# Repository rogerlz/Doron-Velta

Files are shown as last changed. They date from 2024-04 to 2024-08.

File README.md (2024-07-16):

# Doron-Velta

## What's This?

I've never owned a Delta printer, but their unique design and mechanics have always fascinated me. As some of you may know, I contribute to maintaining [Danger-Klipper](https://github.com/DangerKlippers/danger-klipper), which involves testing various configurations and setups. In support of this work, Imac_29 (from the #pasteldenata) generously gifted me an FLSUN Q5. Interestingly, it never even saw the light of day in my home; I disassembled it on the very first day.

This all happened around SMRRF2023, where we humorously speculated that the Voron Design team would never release an official Delta design. What could be a better April Fool's joke than that? So, I went with it.

Originally, the plan was to create an April Fool's prank using the FLSUN Q5, printing parts to make it look like a Voron design. However, I ended up using just the Q5's arms and nothing else. I gathered a collection of spare parts I had lying around, began measuring, and started designing in CAD. After various splits and merges, I had a design reminiscent of the Voron Trident that I was happy enough. It wasn't complete but enough to share with other contributors.

[DoubleT](https://github.com/3DPrintingMods) was immediately on board and decided to build one himself. Within hours of discussing it with me, he had already ordered half of the parts. Interestingly, he managed to get his version printing even before I did.

I want to make it clear that I don't claim to have extensive CAD expertise or experience with Delta printers for this project, so please take my work with a grain of salt. My primary aim was, and remains, to explore Klipper firmware with Delta kinematics.

Yes, the printer works. Yes, it prints. Yes, it's aesthetically pleasing. And yes, it's far from being a perfect design. Most importantly, no, **this is not an official project by Voron Design**.

## **** Disclaimer ****

The toolhead doesn't have the full bed travel. It will hit the panels and/or the belts. New interactions of the printed parts will improve this, but I can't promise it will ever have the full bed travel without a major redesign.
I appreciate any and all the feedback, but I want to ensure everyone understands the design limitations.

## Links

[Doron-Velta Early Bird Kit by FYSETC](https://s.click.aliexpress.com/e/_DejsxX9)\
\
[DV-000 by rogerlz](https://www.reddit.com/r/voroncorexy/comments/1bsr2d7/special_serial_request_dv000_rogerlz/) ([YouTube](https://www.youtube.com/watch?v=DuFxvsZ5HEU))\
[DV-001 by DoubleT](https://www.reddit.com/r/voroncorexy/comments/1bsrmby/special_serial_request_dv001_doublet/) ([YouTube](https://www.youtube.com/watch?v=adXSPTnKe_0))\
[DV-002 by Robert Klotz](https://www.reddit.com/r/voroncorexy/comments/1cw2izk/special_serial_request_dv002_robert_klotz/)\
[DV-003 by Xiar](https://www.reddit.com/r/voroncorexy/comments/1d45y17/special_serial_request_dv_xiar/)\
[DV-004 by Owl47 Bruno Silva](https://discord.com/channels/825469421346226226/1246869064173748285/1246998381964824697)\
[DV-005 by ZombieHedgeDog](https://discord.com/channels/825469421346226226/1246869064173748285/1247178407012208701)
...

## Pictures

 
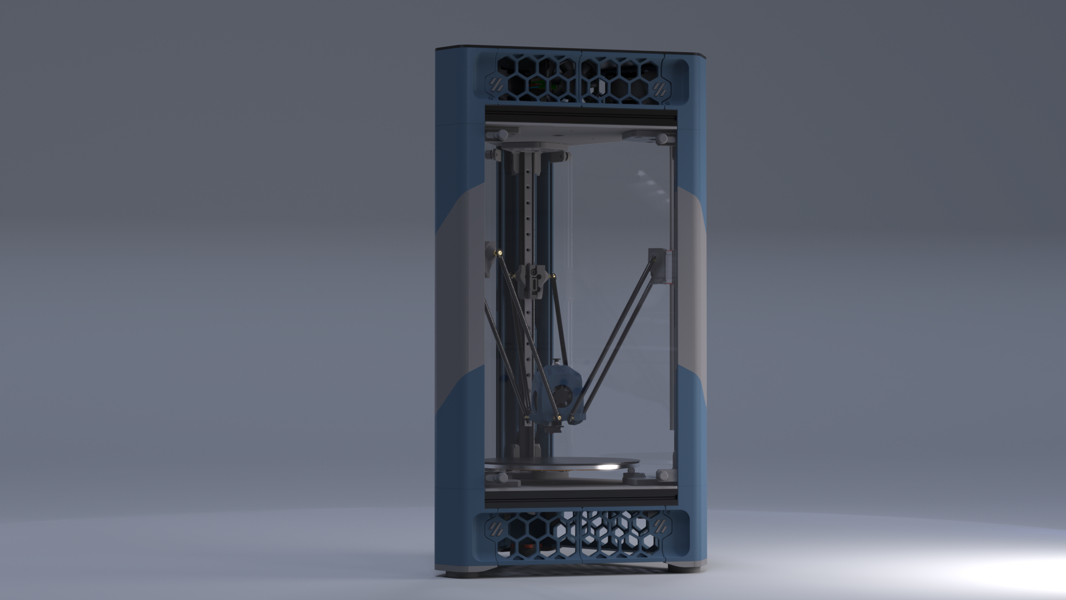
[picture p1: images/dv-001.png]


## Bill of Materials (BOM)
A bill of materials can be found here: [BOM](./BOM.md)

## Changelog

July 13, 2024 (R2 v20)
  - I got an extra ~10mm travel achieved with some improvements on the printed parts. The 2020s moved 5mm to the back, and 2040s moved 5mm to the sides. Almost all printed parts are changing, except the skirts. The only hardware changes are on the ACM panels as they are slightly wider now. The M5x60s are no longer needed.
  - Doron-Velta has a new logo (thanks to @matrixray).
  - I added new skirts with the new logo.
  - There is also a new skirt with a 6020 fan (Thanks to @timmit99 and @seti118 for the fan mount)
  - New UHP-200 mount to compensate the extrusions movement (Thanks to @timmit99)
  - The official toolhead is now [CraneFly by chirpy](https://github.com/chirpy2605/voron/tree/main/general/CraneFly). The MiniSB is hidden in the F3D file, but I won't be making changes to it anymore. Thanks chirpy!
  - Lots of small tweaks here and there based on the community feedback. Thanks everyone.

June 7, 2024 (R1 v30)
  - The interactions are on fire. I invite you to join the DOOMCUBE Discord (#doron_velta_dev) or the Voron Discord (Doron Velta thread) to chat with more people building and modding the design.
  - I got an extra 5mm travel by removing some meat from the belt carriages. That means a new idler mount, new carriage and new endstop mount. No hardware changes.
  - I removed the SKR Pico and Raspberry Pi objects to reduce the cad file size.
  - This makes the Release 1 version with the exported STLs.

June 1, 2024 (v23)
  - Quality of life changes everywhere. Chamfers, fillets, and hole sizes are better now, but nothing major has changed that I would recommend reprinting.
  - @kyleisah was kind enough to create built-in supports for the corner pieces. Thank you!
  - @chirpy is working on an amazing new toolhead. Check it out here [here](https://github.com/chirpy2605/voron/tree/main/general/CraneFly). Thank you!

April 27, 2024 (v16 I think)
  - I modified the Nema17 mounts to include a slot for an MR625 bearing and access to the pulley grub screw. I duplicated them to the bottom for those interested in doing AWD.
  - A new bottom panel and a few missing chamfers were added.

## Thanks to

This was a fun project, and I have a lot of people to thank for, especially the VD (Voron Discord) contributors.

A heartfelt thanks goes out to DoubleT, who dedicated countless hours to CAD work, surpassing even my own time, and to Zruncho, whose guidance, support, and encouragement through direct messages and voice chats were invaluable.

I also want to extend my appreciation to pnewb, clee, hartk, Tetsu, Kyleisah, diem, imac_29 and many others for their support and contributions – you all have my sincerest thanks <3.

I would like to give special acknowledgment to the vendors: [Lab4450.com](https://lab4450.com) for supplying electronic components; ffb (Discord: ffb_9195) and [Seti](https://viperworx.uk) for supplying the PC and ACM panels; and [MandalaRoseWorks](https://mandalaroseworks.com) for the custom-made and beautiful Alu bed.

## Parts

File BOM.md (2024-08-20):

## Doron Velta Bill of Materials (BOM)

### Frame:

| Part | Qty | Notes |
| - | - | - |
| HFSB5-2020-500-TPW  | 3 | Part number is for ordering from Misumi |
| HFSB5-2040-235 | 6 | Part Number is for ordering from Misumi |

### Bed Components:

| Part | Qty | Notes |
| - | - | - |
| 200mmø x 5mm Aluminum Bed | 1 | [MandalaRoseWorks](https://mandalaroseworks.com/collections/doron-velta) / EU folks can ping @owl47_brunosilva on Discord |
| 200mmø PEI Sheet | 1 | [Aliexpress](https://s.click.aliexpress.com/e/_DCjuren) |
| 200mmø Magnetic Sheet | 1 | - |
| M3 x 9mm Ball Screw | 3 | [Aliexpress](https://s.click.aliexpress.com/e/_DkTj85h) |
| 3 x 20mm Steel Dowel Pin | 6 | [Aliexpress](https://s.click.aliexpress.com/e/_DkNIN0x) |

### Motion Components:

| Part | Qty | Notes |
| - | - | - |
| MGN9H 350mm Linear Rail and Carriage | 3 | Any length between 350mm and 400mm fits [Aliexpress](https://s.click.aliexpress.com/e/_Dd2r1B5)|
| GT2 Timing Belt 9mm | ~3 meters | Gates belts are recommended, do not use steel core [Aliexpress](https://s.click.aliexpress.com/e/_Ddi0U3Z) |
| GT2 20T Idler 9mm | 3 | [Aliexpress](https://s.click.aliexpress.com/e/_DmciI0B) |
| 5 x 25mm Steel Dowel Pin | 3 | [Aliexpress](https://s.click.aliexpress.com/e/_DkNIN0x) |
| GT2 20T Pulley 9mm | 3 | [Aliexpress](https://s.click.aliexpress.com/e/_Dd2qIPV) |
| Nema17 Stepper Motors (60mm maximum, 48mm recommended) | 3 | - |
| 210mm Fisheye Rods | 6 | I used: FLSUN Q5 arms [Aliexpress](https://s.click.aliexpress.com/e/_DczHNMX) |
| MR625 Bearing | 3 | Optional for Nema17 with shafts greater than 24+mm |

### Electronics:

| Part | Qty | Notes |
| - | - | - |
| 200W 24V DC Power Supply | 1 | [Meanwell UHP-200-24 Power Supply](https://www.digikey.com/short/hprdfmrv) [Aliexpress](https://s.click.aliexpress.com/e/_DdE9sY7) |
| 170mmø 200W AC Heater | 1 | [Keenovo](https://keenovo.store/collections/standard-keenovo-silicone-heaters/products/keenovo-round-circular-silicone-heater-delta-3d-printer-build-plate-heatbed-heating-pad) |
| IEC320 C14 Inlet | 1 | [DigiKey](https://www.digikey.com/short/z4z73jbr) |
| Solid State Relay | 1 | [Omron SSR](https://www.digikey.com/short/bztzphm9) |
| MCU with 4+ stepper drivers | 1 | [BTT SKR Pico](https://s.click.aliexpress.com/e/_DBLd6hV) /  |
| Omron D2F-L microswitch | 3* | 3 is standard, 4 if you're using [Klicky Probe](https://github.com/jlas1/Klicky-Probe) |

### Printhead:

See [CraneFly by chirpy](https://github.com/chirpy2605/voron/tree/main/general/CraneFly)

### Hardware:
> Most hardware used throughout the design is button head

| Part | Qty | Notes |
| - | - | - |
| M3 x 6 | 40 | - |
| M3 x 8 | 110 | - |
| M3 x 10 | 12 | - |
| M3 x 12 | 10 | - |
| M3 x 16 | 26 | - |
| M3 x 20 | 2 | - |
| M3 x 30 | 2 | - |
| M5 x 8 | 24 | - |
| M5 x 10 | 26 | - |
| M5 x 12 | 36 | - |
| M5 x 16 | 3  | - |
| M5 x 25 | 6 | - |
| M5 Hex Nut | 3 | - |
| M3 Heat Inserts | 50 | - |

### Panels:

| Part | Qty | Notes |
| - | - | - |
| ACM/Acrylic Inner Panels | 2 | [Viper Worx UK](https://www.viperworx.uk/product-category/panels/doron-velta) |
| ACM/Acrylic Bottom Panel | 1 | [Viper Worx UK](https://www.viperworx.uk/product-category/panels/doron-velta) |
| ACM/Acrylic Upper Panel | 1 | [Viper Worx UK](https://www.viperworx.uk/product-category/panels/doron-velta) |
| Acrylic Side Panels | 3 | [Viper Worx UK](https://www.viperworx.uk/product-category/panels/doron-velta) |

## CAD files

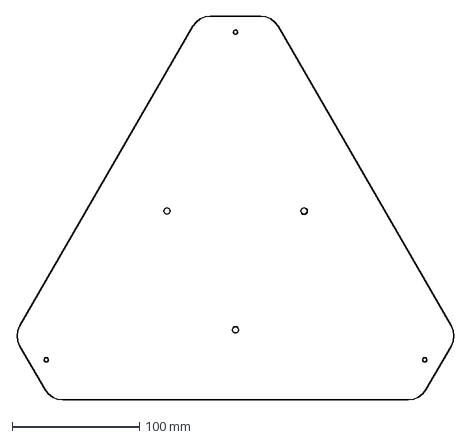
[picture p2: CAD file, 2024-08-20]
DXFs/top_panel_x1.dxf
344.6 x 301.5 mm

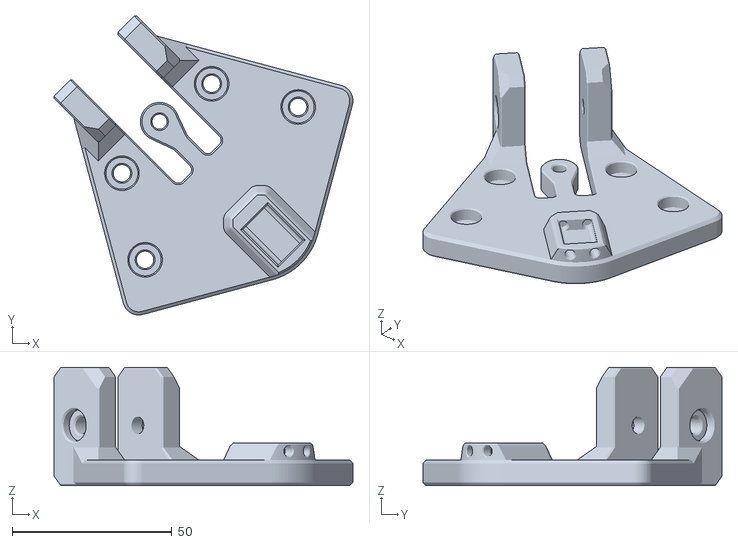
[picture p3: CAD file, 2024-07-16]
STLs/Corners/[a]bed_mount_x3.stl
93.4 x 93.4 x 37.0

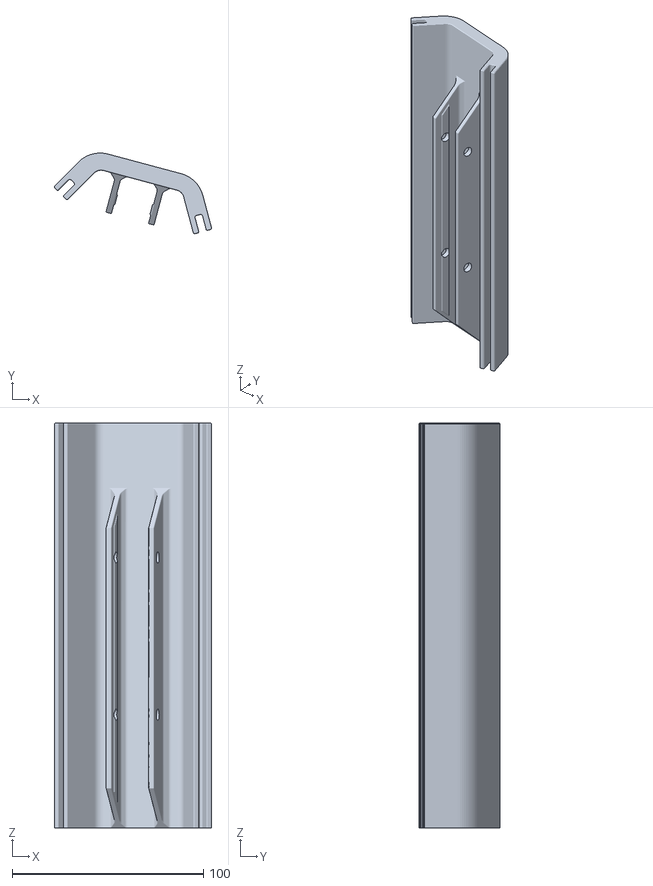
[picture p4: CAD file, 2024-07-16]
STLs/Covers/cover_flat_x2.stl
82.2 x 42.2 x 211.5

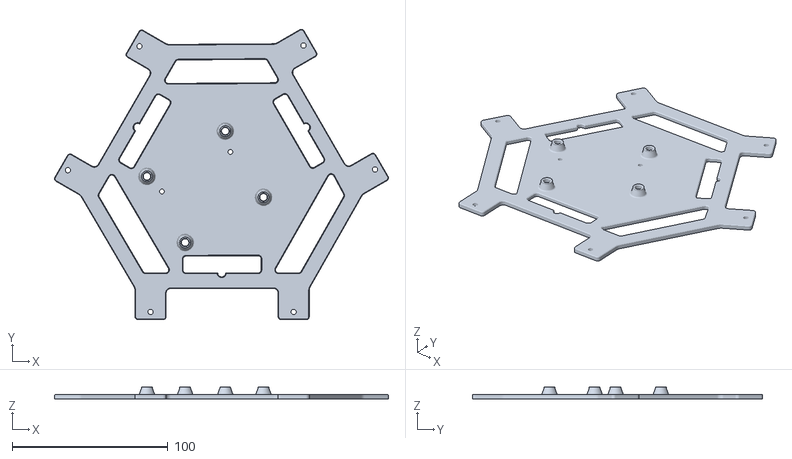
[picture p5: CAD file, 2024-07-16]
STLs/Electronics/skr_pico_mount_x1.stl
214.2 x 186.3 x 8.00

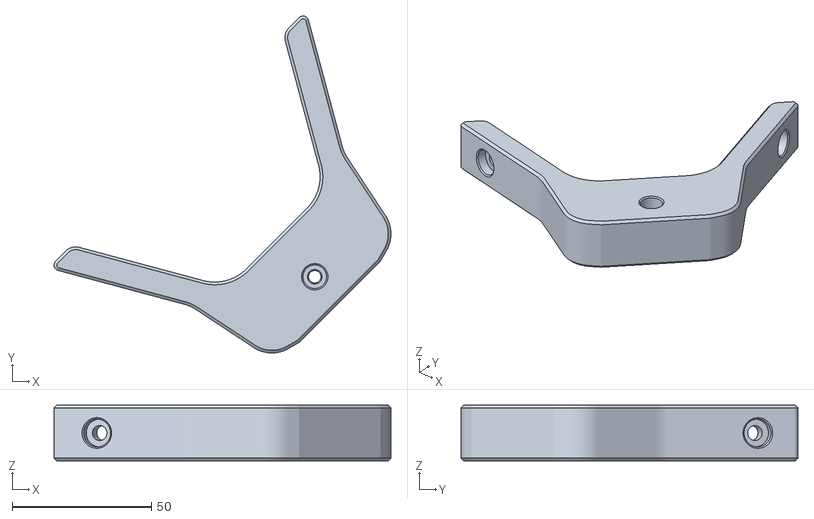
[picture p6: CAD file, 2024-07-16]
STLs/Extruders/sherpa_mount_x1.stl
121.0 x 121.0 x 20.0

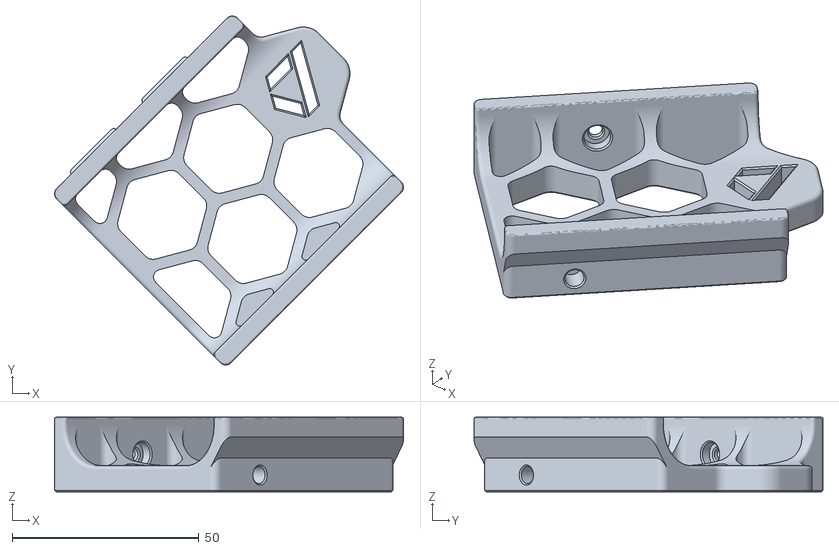
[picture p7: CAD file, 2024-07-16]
STLs/Skirts/DV_Logo/top_skirt_fan_left_dv_x1.stl
93.4 x 93.4 x 20.0

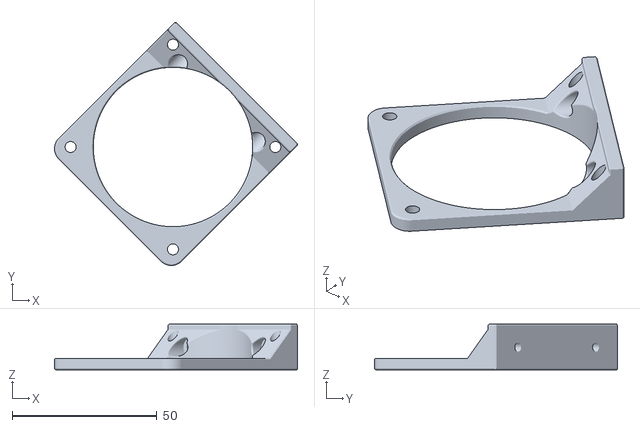
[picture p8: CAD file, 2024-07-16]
STLs/Skirts/fan_mount_x1.stl
83.9 x 83.9 x 15.8

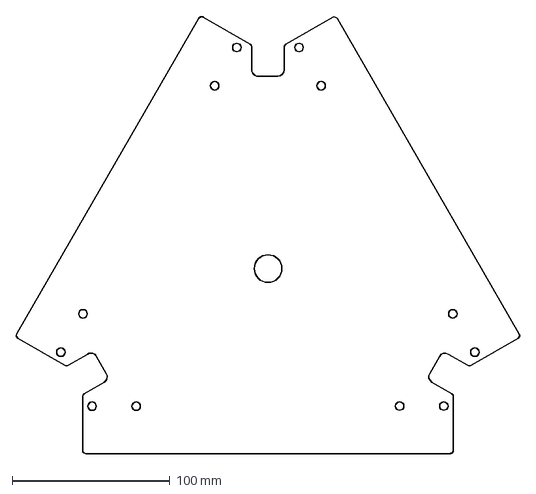
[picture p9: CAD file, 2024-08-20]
DXFs/inner_panel_x2.dxf
319.2 x 277.1 mm

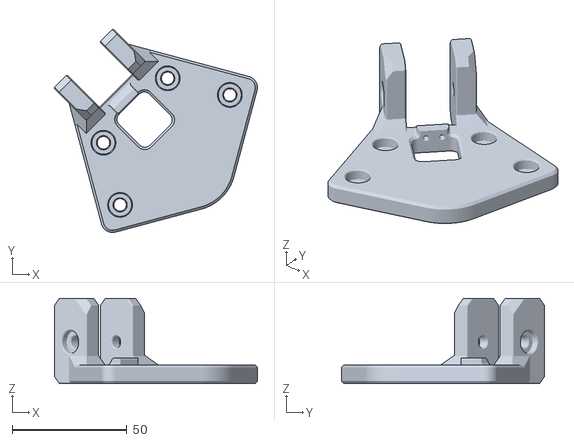
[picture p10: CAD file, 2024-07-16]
STLs/Corners/[a]endstop_mount_x3.stl
88.3 x 88.4 x 37.0

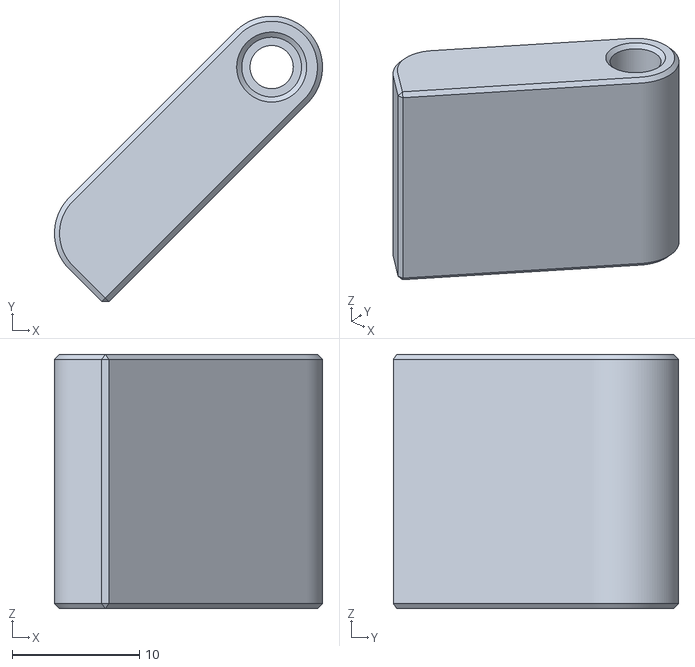
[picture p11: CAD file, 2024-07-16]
STLs/Covers/[a]door_hinge_top_x1.stl
21.1 x 22.5 x 20.0

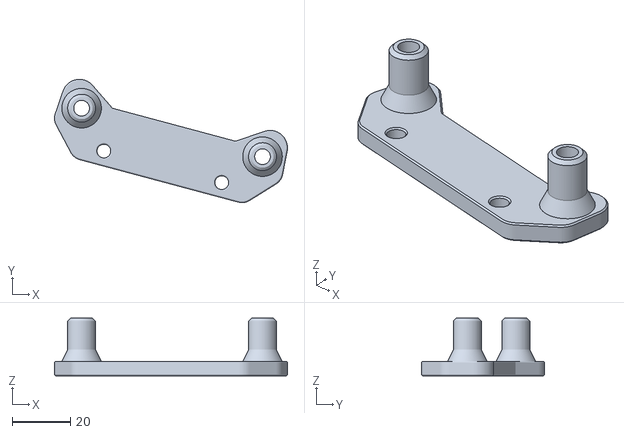
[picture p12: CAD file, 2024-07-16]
STLs/Electronics/uhp200_mount_1_x1.stl
80.2 x 42.4 x 19.9

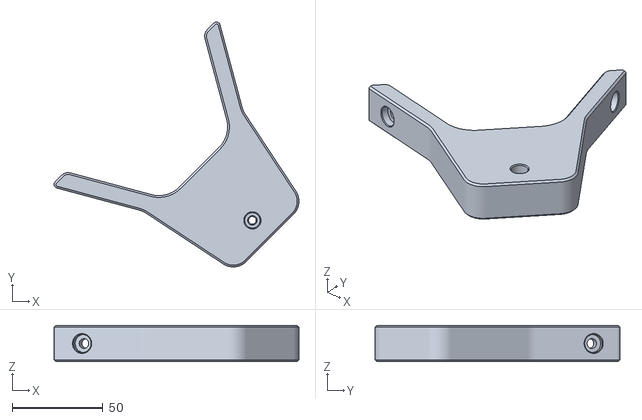
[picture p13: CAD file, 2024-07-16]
STLs/Extruders/g2sa_mount_x1.stl
134.8 x 134.8 x 20.0

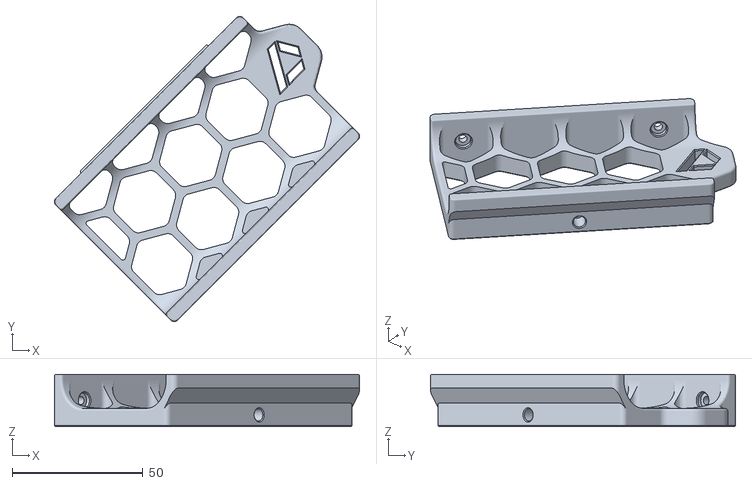
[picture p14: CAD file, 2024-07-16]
STLs/Skirts/DV_Logo/bottom_skirt_dv_right_x2.stl
116.8 x 116.8 x 20.0

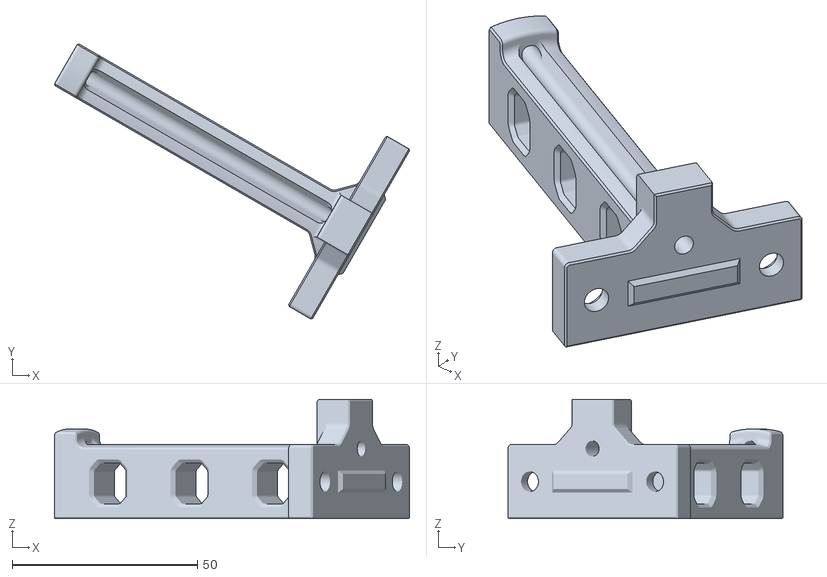
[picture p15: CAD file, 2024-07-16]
STLs/Skirts/spool_holder_x1.stl
95.8 x 74.2 x 32.2

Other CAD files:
STLs/Skirts/VD_Logo/top_skirt_right_vd_x2.stl
STLs/Skirts/VD_Logo/[a]fan_grill_vd_x1.stl
DXFs/bottom_panel_x1.dxf
STLs/Corners/n17_stepper_mount_x3.stl
DXFs/side_panels_x3.dxf
STLs/Corners/[a]belt_tensioner_x3.stl
STLs/Corners/[a]foot_plate_x3.stl
STLs/Corners/belt_carriage_x3.stl
STLs/Corners/idler_mount_pin_x3.stl
STLs/Covers/[a]cover_door_middlebottom_x1.stl
STLs/Covers/[a]cover_door_middletop_x1.stl
STLs/Covers/[a]cover_hinge_middlebottom_x1.stl
STLs/Covers/[a]cover_hinge_middletop_x1.stl
STLs/Covers/[a]door_hinge_bottom_x1.stl
STLs/Covers/cover_door_bottom_x1.stl
STLs/Covers/cover_door_top_x1.stl
STLs/Covers/cover_hinge_bottom_x1.stl
STLs/Covers/cover_hinge_top_x1.stl
STLs/Covers/door_handle_x1.stl
STLs/Electronics/ssr_mount_x1.stl
STLs/Electronics/uhp200_mount_2_x1.stl
STLs/Skirts/DV_Logo/[a]fan_grill_dv_x1.stl
STLs/Skirts/DV_Logo/[a]skirt_dv_logo_x12.stl
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

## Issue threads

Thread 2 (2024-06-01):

BOM update

Life0fBrian, 2024-06-01:
Can you please add the used power inlet to the bom.
Should be `IEC320 C14 inlet` if I'm right.

kyleisah, 2024-06-01:
#3 fixes this issue

kyleisah, 2024-06-01:
Removing the BOM from the readme might be a good idea, and just having a CSV or a separate .md for this would probably be best. I can help you export one from CAD, Roger. 😄

Life0fBrian, 2024-06-01:
I would prefer a .md to be able reading it everywhere.
Thanks for your help.
There should be an update on the 5 mm dowell pins as well to 25 mm length.

rogerlz, 2024-06-01:
thank you both. BOM is now on a separate file, and I fixed the dowel pin length.

Closed 2024-06-01.

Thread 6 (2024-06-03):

STL file

Fearyao, 2024-06-03:
Please provide STL files for 3D printing

rogerlz, 2024-06-08:
They are now available. I did not upload the pieces to mount the panels because there are many color combinations, so I’d recommend you open the CAD to choose which ones you like.

Closed 2024-06-08.

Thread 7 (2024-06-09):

Magnetic ball arms?

visualinventor, 2024-06-09:
This is a well done Voron like design so kudos to you, for not being great at CAD I'd say you're doing really well.
This isn't an issue per se but a curiosity. I'm curious as to why you didn't go with magnetic ball arms instead?

rogerlz, 2024-07-01:
Hey!

Thanks for the feedback.

I think the README explains the reasons. I already had the FLSUN Q5 arms, the design was meant as a meme, and this is my first delta, so I honestly don't know the (dis)advantages over magnetic ball arms.

It is definitely something I'd like to play with at some point and I would happily give feedback on a mod to use them.

Ty
Roger

Closed 2024-07-01.

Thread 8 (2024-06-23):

Bolts for feet too short

AxMod3DPrint, 2024-06-23:
Hi Seti here,

I'm just checking fixings and with the feet in the CAD the M5x60 is too short, this needs to be at least an M5x70 to engage properly with the extrusion. I have printed mine, but ripped the model straight from the CAD, so I would assume that the standard Voron v2/Trident feet will have the same issue.

rogerlz, 2024-07-01:
Hey!

Thanks for the feedback. You are the first one I hear about needing a m5x70. Anyway, those screws don't play any vital role in the structure. They are only meant to keep the feet in place and help assemble the 2020s straight.

The new R2 version now uses m5x16.

Ty
Roger

Closed 2024-07-01.

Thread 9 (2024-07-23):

Sensorless?

hreality, 2024-07-23:
Do you know of or have any information to make this sensorless for A, B, C?

yzeroy, 2024-07-26:
As official BTT user guide states, just use jumper caps as in screenshot, unplug endstop wires from board and change klipper config as any for other kinematics. BUT, keep in mind that sensorless homing is not as precise as fysical endstops, repeatability is not as precise.

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

[https://github.com/bigtreetech/SKR-Pico](url)

hreality, 2024-07-31:
Thank you for the response.  While not 'this' delta I did use you as a template and discovered that variations in endstops can cause exaggerated artifacts in print.  That being said, using a sensorless option where each endstop is a 'percieved' balance is an even worse idea.

Closed 2024-07-31.

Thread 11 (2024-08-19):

Alternative source for 210mm fisheye rods

kozross, 2024-08-19:
The linked ones are no longer available to buy.

rogerlz, 2024-08-20:
link is fixed. thanks

Closed 2024-08-20.

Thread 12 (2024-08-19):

Clarification on rail length

kozross, 2024-08-19:
In the BOM, it says that "350-400mm length of rail is recommended". What does this mean exactly? Normally rail lengths for printer BOMs are fairly specific: how should this provided range be interpreted?

rogerlz, 2024-08-20:
It means that anything between 350mm and 400mm will fit.
Use what you have or buy 350mm. I will clarify in the BOM. Thanks

Closed 2024-08-20.

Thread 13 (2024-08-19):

What length of NEMA17 motors will fit?

kozross, 2024-08-19:
The BOM specifies NEMA17s, but doesn't state what length will fit the build.

Killajoedotcom, 2024-08-19:
There is enough room up top to accept up to a 60mm length Nema 17. It would be tight, but could be done. Standard 48mm motors work without issues.

kozross, 2024-08-19:
We should add this information to the BOM. I can send a PR.

Closed 2024-08-20.

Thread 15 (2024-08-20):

Purpose of small bed plate holes

kozross, 2024-08-20:
The aluminium bed plate has three small (~2.4mm diameter) holes in it, as highlighted below:

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

What is the purpose of these holes? According to the CAD model, they don't attach to anything, and they're only big enough for M2 hardware.

rogerlz, 2024-08-20:
they are m3 tapped holes, and you can use them for ground, thermal fuse and an extra thermistor

Closed 2024-08-20.

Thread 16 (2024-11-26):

print ABS

maxiro-samurai, 2024-11-26:
I want to know if this machine can print ABS? There are two holes in top and bottom panels, so it's not completely sealed.

yebo29, 2025-03-13:
I haven't built one yet, but I'm assuming that as long as the chamber can have stable temps and prevent drafts, then I would say yes. Remember that if printing ABS to have proper ventilation, specially if it's not completely sealed.

MandicReally, 2025-03-13:
If fully enclosed the Doron loses a lot of build volume. See Modbot's video on the matter. https://youtu.be/vrZ0k-R8vF8?si=H5S7AYq_Hc_cyHbO&t=163

Closed 2025-04-28.

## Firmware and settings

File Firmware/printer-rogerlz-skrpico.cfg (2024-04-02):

[include mainsail.cfg]

[virtual_sdcard]
path: /home/pi/printer_data/gcodes
on_error_gcode: CANCEL_PRINT

[respond]

[mcu]
serial: /dev/serial/by-id/usb-Klipper_rp2040_45503571288E5E98-if00

[printer]
kinematics: delta
max_velocity: 50
max_accel: 1500
max_z_velocity: 50
delta_radius: 100.922298
print_radius: 100

[danger_options]
log_statistics: False
log_config_file_at_startup: False
log_bed_mesh_at_startup: False
adc_ignore_limits: True

[delta_calibrate]
radius: 80
horizontal_move_z: 15

[heater_bed]
heater_pin: gpio21
sensor_type: Generic 3950
sensor_pin: gpio26
max_power: 1
min_temp: -100
max_temp: 130
control: pid
pid_kp: 17.743
pid_ki: 0.288
pid_kd: 273.017

[bed_mesh]
speed: 50
horizontal_move_z: 15
mesh_radius: 70
mesh_origin: 0,0
round_probe_count: 5
fade_start: 1.0
fade_end: 6.0
split_delta_z: .025
move_check_distance: 5.0
mesh_pps: 2,2
algorithm: bicubic

[extruder]
step_pin: gpio14
dir_pin: gpio13
enable_pin: !gpio15
microsteps: 16

# Galileo 2
rotation_distance: 47.088
gear_ratio: 9:1

nozzle_diameter: 0.4
filament_diameter: 1.75
heater_pin: gpio23
sensor_pin: gpio27
sensor_type: PT1000
min_temp: 10
max_temp: 350
min_extrude_temp: 20
control: pid
pid_kp: 30.684
pid_ki: 2.188
pid_kd: 107.585

[tmc2209 extruder]
uart_pin: gpio9
tx_pin: gpio8
uart_address: 3
interpolate: False
run_current: 0.8

[temperature_sensor Pi]
sensor_type: temperature_host
min_temp: 1
max_temp: 100

[temperature_sensor SKRPico]
sensor_type: temperature_mcu
min_temp: 0
max_temp: 100

[fan]
pin: gpio17
kick_start_time: 0.25
cycle_time: 0.10

[heater_fan hotend_fan]
pin: gpio18
heater: extruder
heater_temp: 50.0
kick_start_time: 0.25
cycle_time: 0.10

[probe]
pin: ^gpio16
x_offset: 0
y_offset: 19.45
z_offset: 10.450
speed: 10
samples: 3
samples_result: median
sample_retract_dist: 3
samples_tolerance: 0.01
samples_tolerance_retries: 5

# connected to X
[stepper_a]
step_pin: gpio11
dir_pin: gpio10
enable_pin: !gpio12
rotation_distance: 40
gear_ratio: 9:1
microsteps: 32
endstop_pin: ^gpio4
homing_speed: 20
homing_retract_dist: 5
homing_retract_speed: 10
position_endstop: 165.050109
angle: 209.197966
arm_length: 215

# connected to z1
[stepper_b]
step_pin: gpio19
dir_pin: gpio28
enable_pin: !gpio2
rotation_distance: 40
gear_ratio: 9:1
microsteps: 32
endstop_pin: ^gpio25
position_endstop: 166.205031
angle: 328.568677
arm_length: 215

# connected to y
[stepper_c]
step_pin: gpio6
dir_pin: gpio5
enable_pin: !gpio7
rotation_distance: 40
gear_ratio: 9:1
microsteps: 32
endstop_pin: ^gpio3
position_endstop: 164.911920
angle: 90
arm_length: 215

[tmc2209 stepper_a]
uart_pin: gpio9
tx_pin: gpio8
uart_address: 0
run_current: 0.9
interpolate: false

[tmc2209 stepper_b]
uart_pin: gpio9
tx_pin: gpio8
uart_address: 1
run_current: 0.9
interpolate: false

[tmc2209 stepper_c]
uart_pin: gpio9
tx_pin: gpio8
uart_address: 2
run_current: 0.9
interpolate: false

[endstop_phase stepper_a]
trigger_phase = 24/128

[endstop_phase stepper_b]
trigger_phase = 101/128

[endstop_phase stepper_c]
trigger_phase = 33/128

[autotune_tmc stepper_a]
motor: ldo-36sth20-1004ahg
tuning_goal: performance
voltage: 24

[autotune_tmc stepper_b]
motor: ldo-36sth20-1004ahg
tuning_goal: performance
voltage: 24

[autotune_tmc stepper_c]
motor: ldo-36sth20-1004ahg
tuning_goal: performance
voltage: 24

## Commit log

2024-03-13 adds a wip bom to the readme
2024-03-13 upload printer-rogerlz-m5p
    [printer-rogerlz-m5p.cfg]
2024-04-02 first public version
    [printer-rogerlz-m5p.cfg, printer-rogerlz-skrpico.cfg]
2024-05-12 fix ball screws size
2024-06-01 Update README.md
    Add inlet to BOM section
2024-06-01 Update README.md
    Remove BOM section to be used in a separate file
2024-06-01 Update README.md
    correct link to BOM
2024-06-01 update bom
2024-06-01 v23 cad
    [MotorMountGrubAccess.step]
2024-06-07 stls, r1 version
    [[a]bed_mount_x3.stl, [a]belt_tensioner_x3.stl, [a]bottom_corner_base_plate_x3.stl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]
2024-07-16 r2 version
    [MotorMountGrubAccess.step, [a]bed_mount_x3.stl, [a]belt_tensioner_x3.stl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]
2024-08-19 Add note on motor size
2024-08-20 update rail size
2024-08-20 dxf files
    [bottom_panel_x1.dxf, inner_panel_x2.dxf, side_panels_x3.dxf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]
